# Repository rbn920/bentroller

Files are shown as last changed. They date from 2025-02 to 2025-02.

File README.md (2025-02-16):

# Bentroller V2
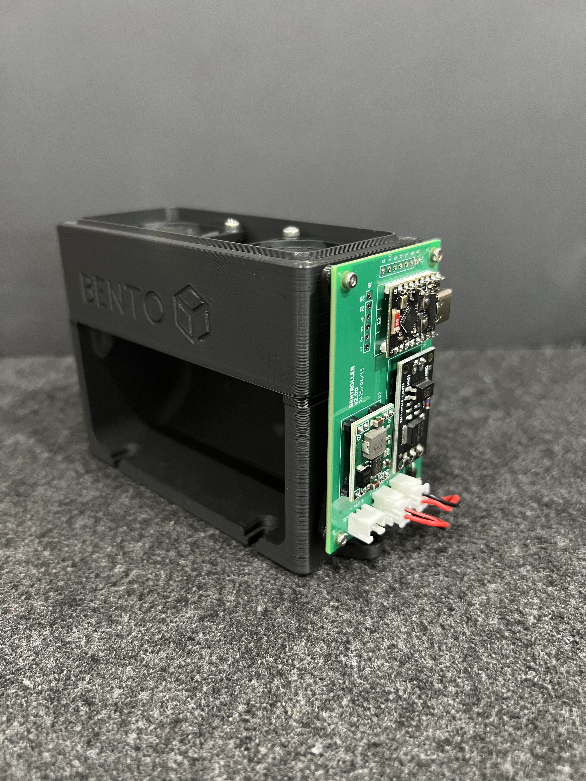
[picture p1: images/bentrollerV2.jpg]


PCB design for controlling the populer BentoBox air filter. The PCB uses an ESP32 to simple control of the Bentobox in Home Assistant. This project is aimed primary for when the BentoBox is used in a Bambu Labs printer due to the closed firmware.

The design goals were as follows:
- Use 24v supply from the printers PSU.
- Control the fans remoteley from Home Assistant.

## Bill of Materials (BOM)

| Qty | Item | Notes |
| --- | --- | --- |
| 1 | ESP32-C3 Super Mini | |
| 1 | MP1584 voltage converter module (buck converter) | Preset to 3v is preferred but adjustable is fine. |
| 1 | D4184 MOSFET Control Module | Found [here](https://protosupplies.com/product/d4184-mosfet-control-module/) |
| 1 | 1N5819 Diode | |
| 3 | 2-pin JST-HX through hole connectors | |
| 4 | M2x6 SHCS | These are for mounting the PCB to the BentoBox. |

## Printed Parts
There are parts to print in the stl folder to mount the board to the side of the BentoBox. It is a bit hacky but it works. It gets sandwiched between the fan and duct portions of the BentoBox. Print 1 of each mouth part and 4 spacers.

## Changes from V2
I never published V1. I built it and imediatly updated it but the following is a list if changes made:
- Went from an ESP32-S2 to ESP32-C3. I had a handfull of S2 boards so I used it but changed to the C3 because I only needed 1 GPIO and it is more compact.
- Voltage input on the V1 used a screw terminal. V2 moved to a JST-HX.
- V2 makes all pins of the C3 available in case anyone decides to make on of these and comes up for a clever use for the additional pins.

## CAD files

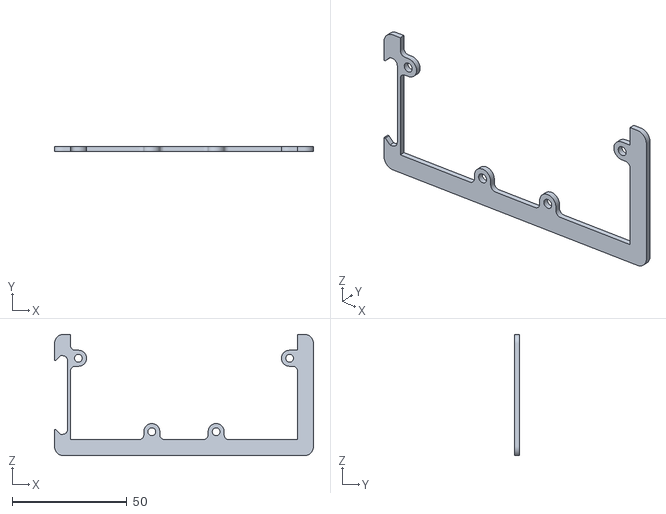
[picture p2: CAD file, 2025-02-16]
stls/bentroller_filtermount_1.stl
112.8 x 2.00 x 52.8

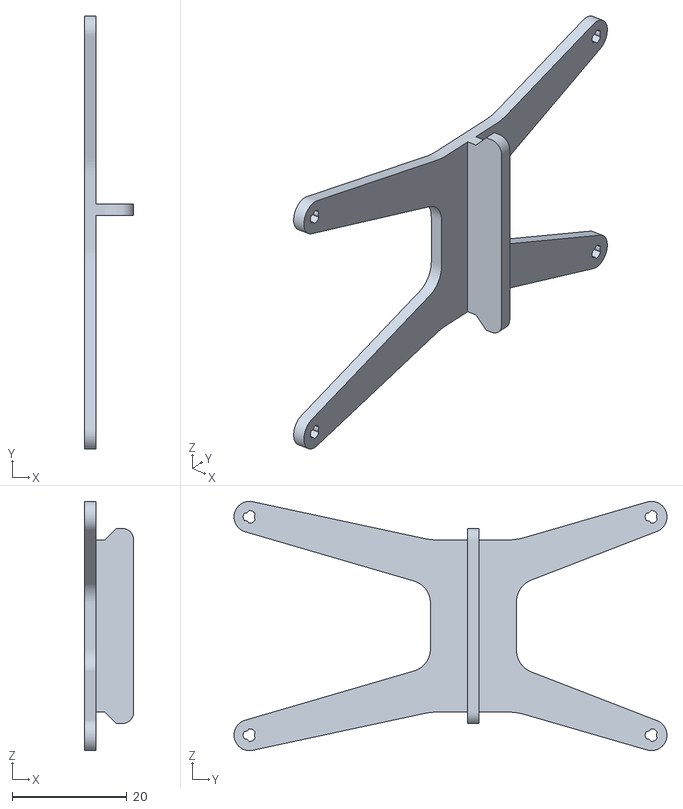
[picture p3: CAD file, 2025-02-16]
stls/bentroller_boardmount_1.stl
8.60 x 75.4 x 43.4

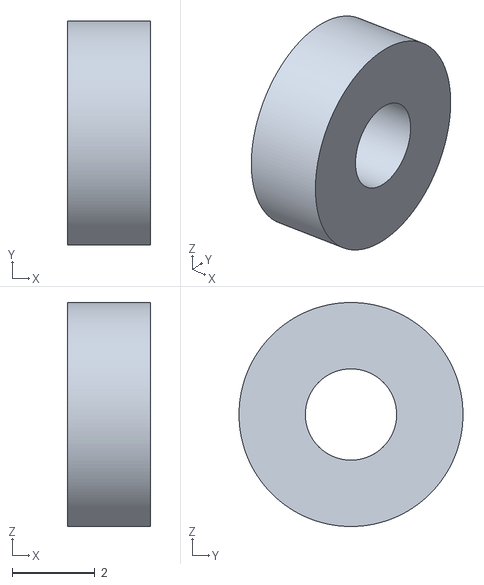
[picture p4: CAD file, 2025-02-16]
stls/bentoller_washer_4.stl
2.00 x 5.40 x 5.40

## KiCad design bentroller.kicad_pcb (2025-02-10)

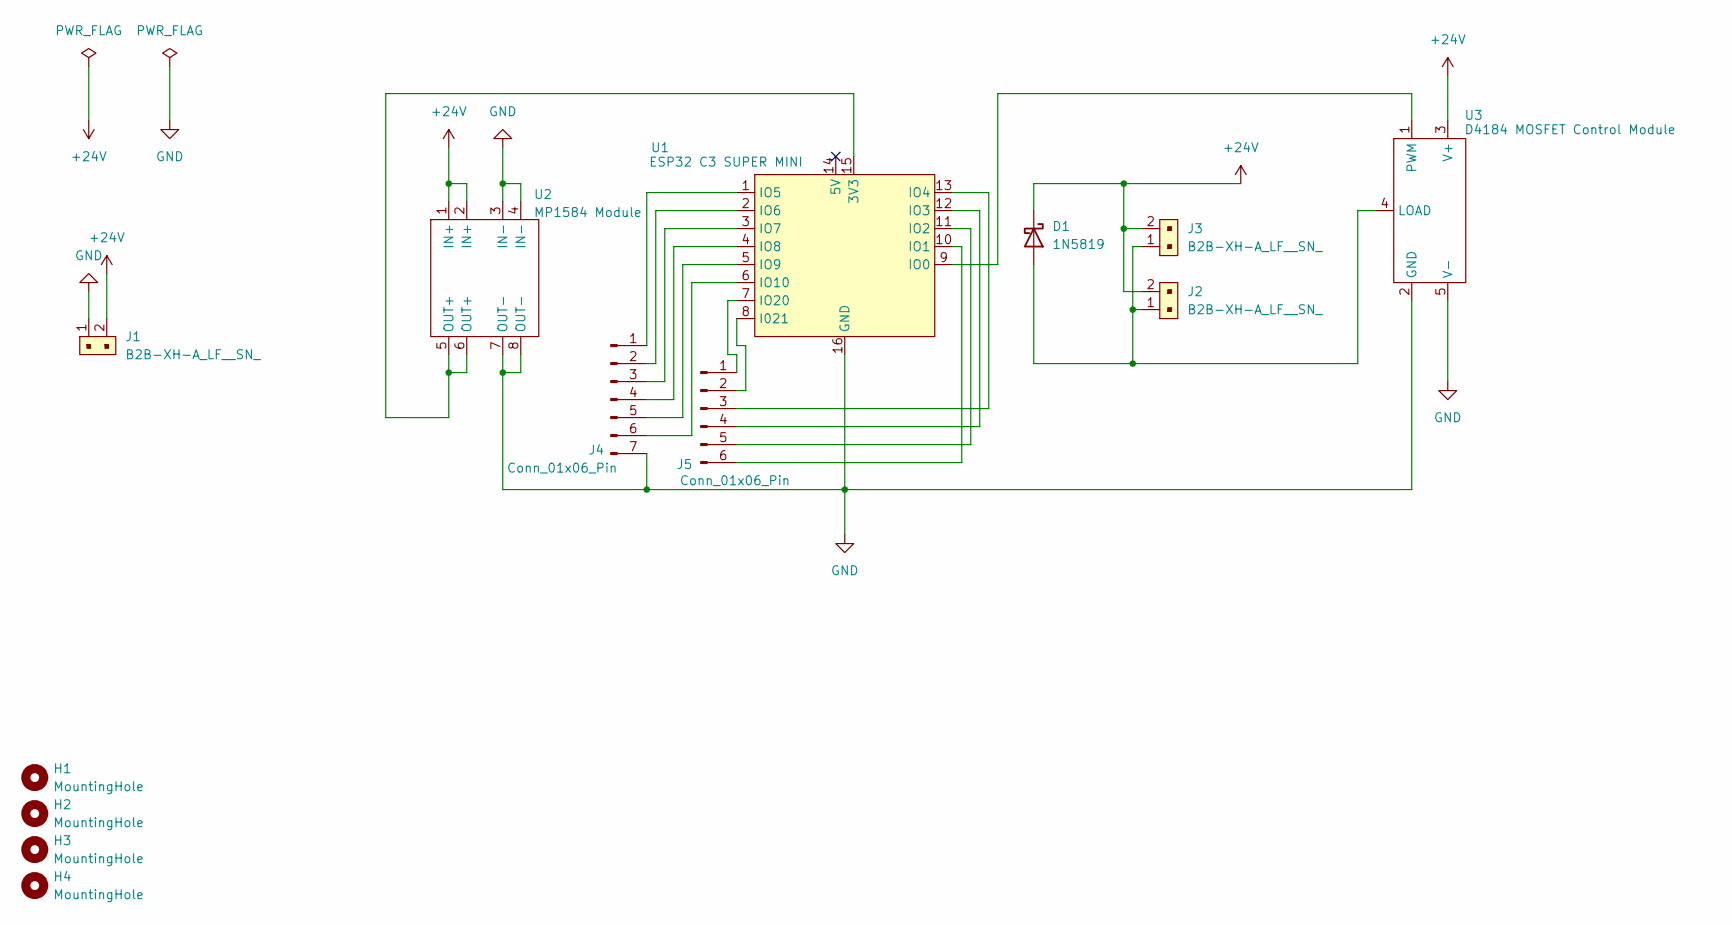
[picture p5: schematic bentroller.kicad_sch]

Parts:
D1: 1N5819; D_DO-41_SOD81_P10.16mm_Horizontal
H1, H2, H3, H4: MountingHole; MountingHole_2.2mm_M2
J1, J2, J3: B2B-XH-A_LF__SN_; PinHeader_1x2_P2.5mm_Drill1.1mm; MPN B2B-XH-A(LF)(SN); Digi-Key_PN 455-2247-ND
J4: Conn_01x06_Pin; PinHeader_1x07_P2.54mm_Vertical
J5: Conn_01x06_Pin; PinHeader_1x06_P2.54mm_Vertical
U1: ESP32 C3 SUPER MINI; ESP32_C3_Super_Mini
U2: MP1584 Module
U3: D4184 MOSFET Control Module

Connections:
+24V: D1.1 (K), J1.2, J2.2, J3.2, U2.1 (IN+), U2.2 (IN+), U3.3 (V+)
GND: J1.1, J4.7, U1.16 (GND), U2.3 (IN-), U2.4 (IN-), U2.7 (OUT-), U2.8 (OUT-), U3.2 (GND), U3.5 (V-)
unnamed: D1.2 (A), J2.1, J3.1, U3.4 (LOAD)
unnamed: J4.1, U1.1 (IO5)
unnamed: J4.2, U1.2 (IO6)
unnamed: J4.3, U1.3 (IO7)
unnamed: J4.4, U1.4 (IO8)
unnamed: J4.5, U1.5 (IO9)
unnamed: J4.6, U1.6 (IO10)
unnamed: J5.1, U1.7 (IO20)
unnamed: J5.2, U1.8 (I021)
unnamed: J5.3, U1.13 (IO4)
unnamed: J5.4, U1.12 (IO3)
unnamed: J5.5, U1.11 (IO2)
unnamed: J5.6, U1.10 (IO1)
unnamed: U1.15 (3V3), U2.5 (OUT+), U2.6 (OUT+)
unnamed: U1.9 (IO0), U3.1 (PWM)

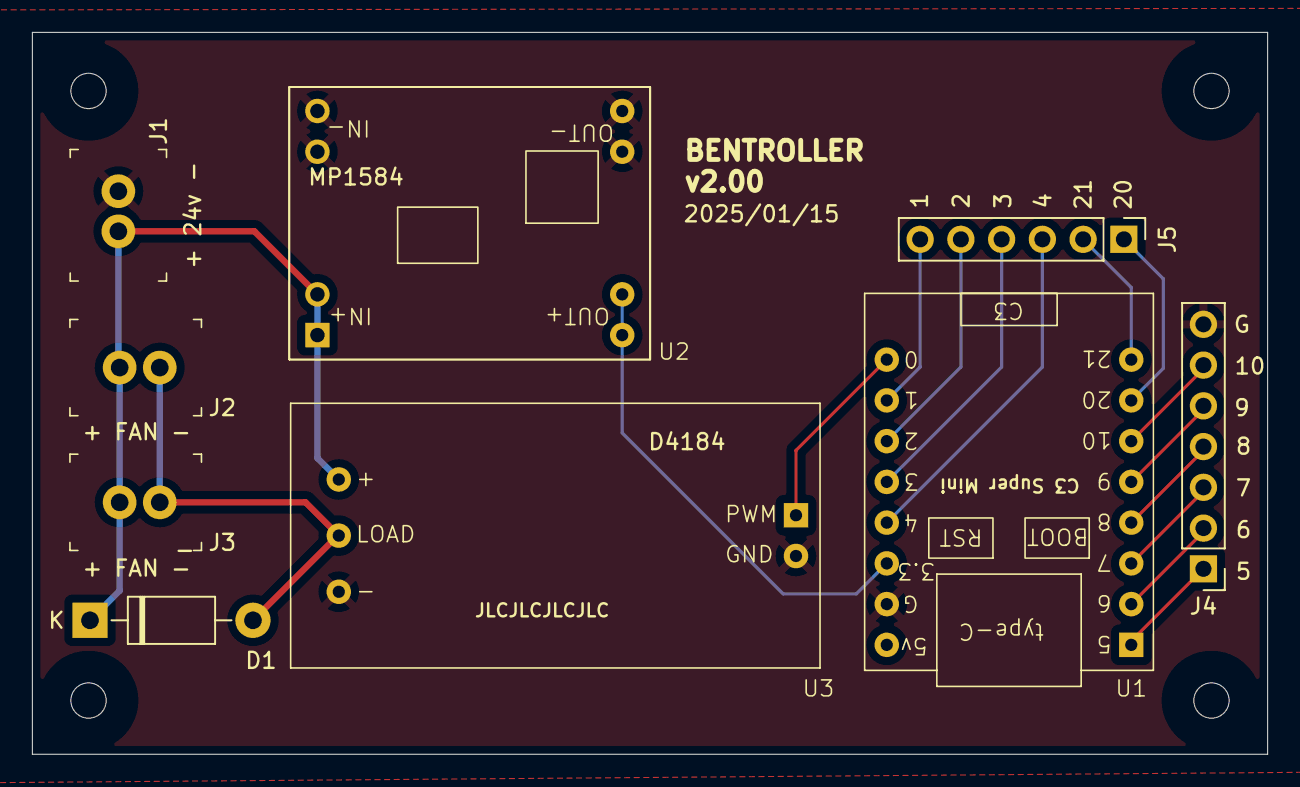
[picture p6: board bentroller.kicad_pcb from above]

Board: 4 copper layers, 77.0 x 45.0 mm, 13 parts (0 on the bottom side), 17 nets.
